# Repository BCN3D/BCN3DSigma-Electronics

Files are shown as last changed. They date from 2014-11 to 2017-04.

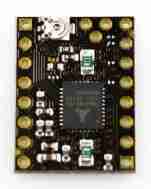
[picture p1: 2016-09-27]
Silent Stepper Driver 4L/Documentation/SilentStepStick-master/hardware/SilentStepStick_v11.jpg

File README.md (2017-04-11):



# BCN3D Electronics

This repository will hold all the information about the Electronics of the BCN3D Sigma.

As a declared Open Source organization, it's in our mission to release all the original design files to you to be able to learn, reuse and improve. Open Source not only means code, it also concerns hardware.

We've managed to design and manufacture our custom Electronics for the BCN3D Sigma in many ways thanks to the community and other Open Source Hardware projects.
BCN3D Electronics is a mashup between the [Ultimaker 2 Board](https://github.com/Ultimaker/Ultimaker2) , the [Megatronics v3.0](http://reprap.org/wiki/Megatronics_3.0) and some others...

## Design concept

The BCN3D Electronics is intended to be modular and custom fitted in our BCN3D Sigma 3D printer and that's why we made some design decisions.

1. Stepper drivers out of the Mainboard. As the drivers generate quite a lot of heat, we've moved them nearest as possible to the corresponding stepper motor. If one fails, you just have to replace a cheap stepper driver board. This way, we've managed to fit an entire electronics system without a fan.
2. FFC's everywhere. The BCN3D Sigma is an Independent Dual Extruder Printer so the Electronics supports 6  Axis of movement. Thats a lot of wires and wires takes some precious space. We decided to go with a Flat Flexible Cable solution that keeps things organized and it's faster to assemble.
3. 24VDC Power Supply. The performance improves as the whole Electronics run cooler while maintaining a very low voltage system.  
4. Full Color Resistive Touch Screen. The electronics is compatible with 4D Systems Displays out of the box. We think the user should interact with an intuitive interface to be able to use the printer easily even without previous experience in 3D printing.

## Boards

+ **Mainboard:** This board holds the microcontroller, the 5V switching power supply, the power outputs and the thermistor inputs. It has a USB interface for upgrading the firmware and communicating with the printer via serial port.
+ **Stepper Driver:** We carry the well-known DRV8825 stepper driver from Texas Instruments. It's able to supply plenty of power for all the types of stepper motors in the BCN3D Sigma.
+ **Extruder Board:** It's a simple interconnection board between the Mainboard and the components of the hotend assembly. With just one Flat Flexible Cable you the microcontroller has control over the hotend, the thermistor and endstop readings and the layer fan.
+ **Heated Bed:** As the platform size of the BCN3D Sigma is quite big, we've made a custom A4 size heated bed to achieve the performance required. It can heat up to 100ºC in about 6-8 minutes and keep that temperature for long period of times.
+ **SD Reader:** We've design our own SD Reader module with better signal integrity and better power supply requirements. This board has been designed entirely in [KiCAD Open Source software](http://kicad-pcb.org/). 

## Production

We strongly believe that using high quality components has an effect on the electronics performance as well as in the printer performance.

This is why we ensure components quality and control of the production process by designing and manufacturing in Barcelona. In this manner we iterate faster, reducing time to market.

Being in control of all the supply chain allows us to optimize designs and reduce costs.

## Contributing

If you own a BCN3D Sigma and electronics is your thing, feel free to post an [issue](https://github.com/BCN3D/BCN3D-Electronics/issues). We know this is still an 8-bit platform but we're working on optimizing it to the max and thinking in the next generation of 3D Printing Electronics. Always Open Source.

### License

Under the **LICENSE** folder you'll find all the information about the license. We've chosen CERN Open Hardware License and you must follow the guidelines as we had. All the documentation is available to you to study it, modify it and share it.
In addition, if modifications are made and distributed, it must be under the same licence conditions – this is the ‘persistent’ nature of the licence, which ensures that the whole community will continue benefiting from improvements, in the sense that everyone will in turn be able to make modifications to these improvements.

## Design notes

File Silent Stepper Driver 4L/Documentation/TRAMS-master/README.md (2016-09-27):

# TRAMS
TRINAMIC ReRrap Arduino Mega Shield, Reference Design for 3D Printing with 4x TMC5130

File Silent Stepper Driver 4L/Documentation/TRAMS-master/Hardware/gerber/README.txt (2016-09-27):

TRAMS v0.91

4 Layer PCB
35 um Copper
1.6mm thickness

Do not buy and assemble D2, D4, D6. 
Only D5 is needed.

Do not assemble all THT parts but ship them with the PCBs.

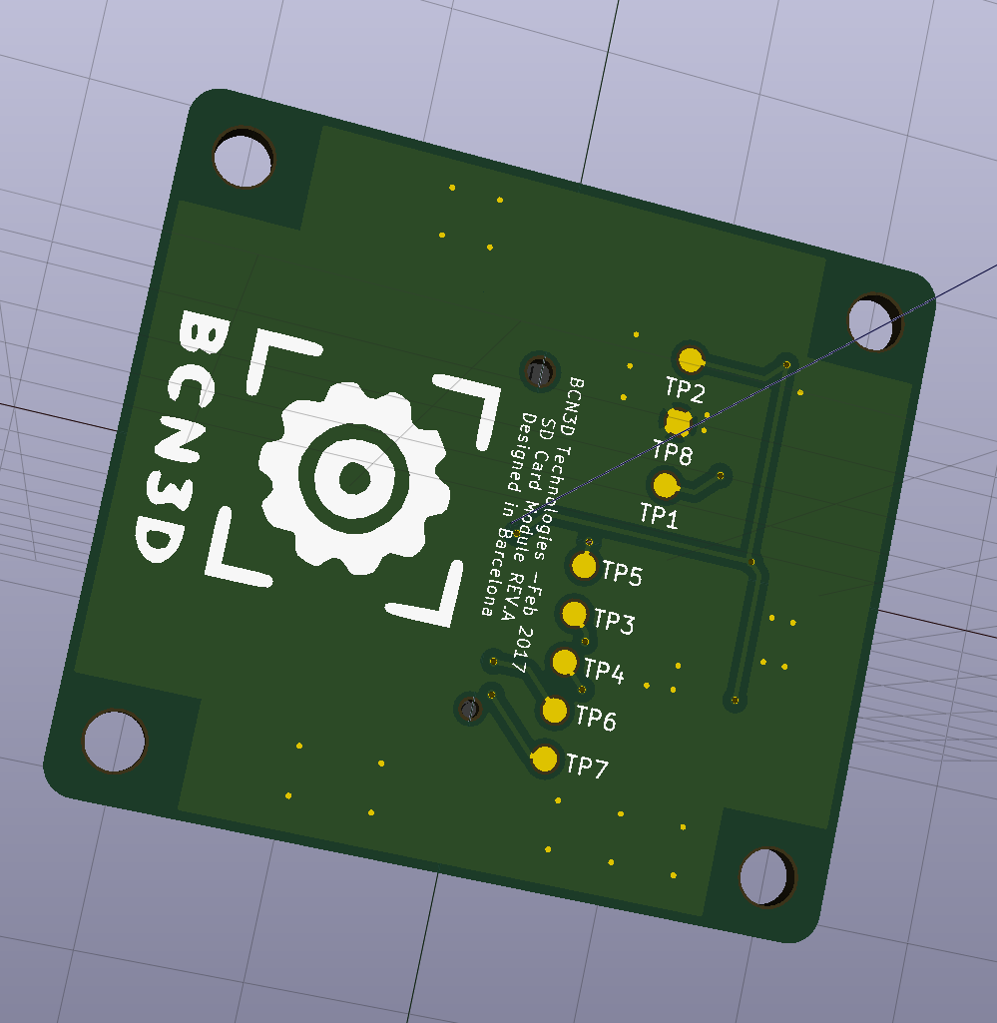
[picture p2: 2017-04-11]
SD Reader/IMG/3D_Back.PNG

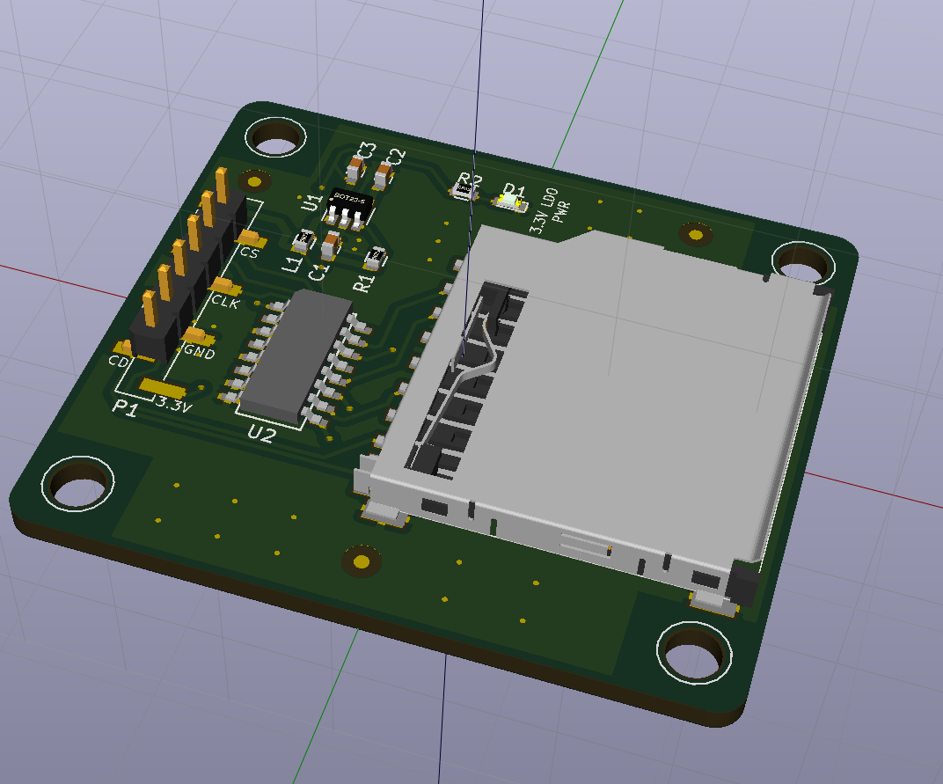
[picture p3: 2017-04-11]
SD Reader/IMG/3D_Front.PNG

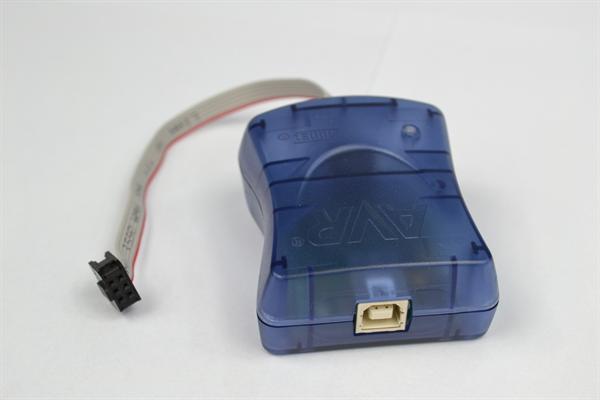
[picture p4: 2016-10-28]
img/avrispmkii.jpg

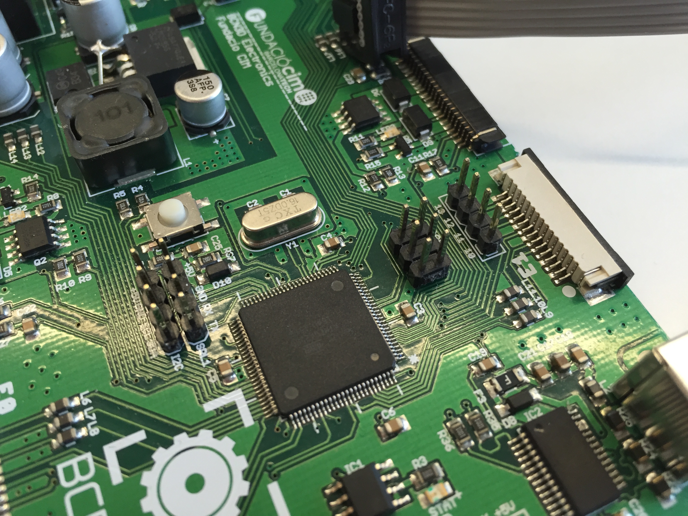
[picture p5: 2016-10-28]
img/mainboard.JPG

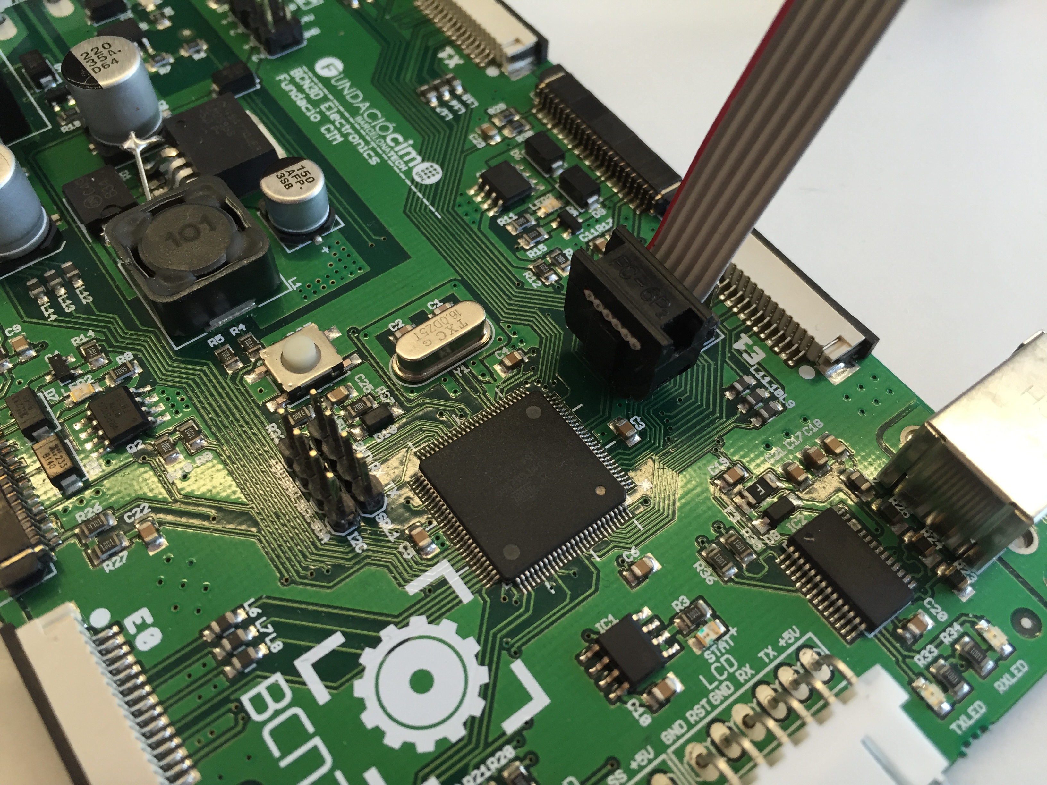
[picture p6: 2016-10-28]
img/mainboardwithcable.JPG

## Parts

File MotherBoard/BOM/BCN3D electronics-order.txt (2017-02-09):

Order list for C:/Users/mcobler/Documents/eagle/BCN3D Electronics/MotherBoard/BCN3D electronics.sch
Exported from EAGLE with DesignLink

Quantity	Value	Package	Order code	Manufacturer	Manuf. Code	Availability	Price (from)	Description
2		JP2Q	unknown					
5		1X04	unknown					
1	ATMEGA2560-16AU	QFP50P1600X1600X120-100N	1288330	ATMEL	ATMEGA2560-16AU	640	8.67	ATMEL - ATMEGA2560-16AU - MCU, 8BIT, ATMEGA, 16MHZ, TQFP-100
2	22p	C0805	2332763	AVX	08055A220KAT2A	38475	0.02	AVX - 08055A220KAT2A - COND, CERÁ MULT, C0G/NP0, 22PF, 50V 0805
8	100n	C0805	499687	AVX	08055C104KAT2A	231426	0.0113	AVX - 08055C104KAT2A - COND, CERÁ MULT, X7R, 100NF, 50V, 0805
1	150UF	CAPAE660X610N	1539463	PANASONIC ELECTRONIC COMPONENTS	EEEFP1A151AP	1011	0.158	PANASONIC ELECTRONIC COMPONENTS - EEEFP1A151AP - COND, ELEC ALUM, 150UF, 10V, SMD
1	220u	UD-8X10_NICHICON	2326175	PANASONIC ELECTRONIC COMPONENTS	EEE1VA221UAP	2654	0.176	PANASONIC ELECTRONIC COMPONENTS - EEE1VA221UAP - COND, ELEC ALUM, 220UF, 35V, SMD
5	0.1u	C0805	499687	AVX	08055C104KAT2A	231426	0.0113	AVX - 08055C104KAT2A - COND, CERÁ MULT, X7R, 100NF, 50V, 0805
2	100u	UD-8X10_NICHICON	1244377	PANASONIC ELECTRONIC COMPONENTS	EEEFC1V101AP	2580	0.292	PANASONIC ELECTRONIC COMPONENTS - EEEFC1V101AP - COND, ELEC ALUM, 100UF, 35V, SMD
2	10u	C1210K	1735537	MURATA	GRM32ER7YA106KA12L	7393	0.556	MURATA - GRM32ER7YA106KA12L - COND, CERÁ MULT, X7R, 10UF, 35V, 1210
1	4.7u	C0805	1833871	AVX	06035C103JAT2A	39173	0.0216	AVX - 06035C103JAT2A - COND, CERÁ MULT, X7R, 10NF, 50V, 0603
2	10n	C0805	499225	AVX	08055C103KAT2A	135923	0.0113	AVX - 08055C103KAT2A - COND, CERÁ MULT, X7R, 10NF, 50V, 0805
1		SMC	9557377	ON SEMICONDUCTOR	MBRS340T3G	44451	0.135	ON SEMICONDUCTOR - MBRS340T3G - DIODE, SCHOTTKY, 3A, 40V, SMC
7	MBRA140	SMA-DIODE	1843670	DIODES INC.	B140-13-F	52776	0.0309	DIODES INC. - B140-13-F - DIODO, SCHOTTKY, 40V, 1A, DO-214AC
2	MBR0520LT	SOD123	2284096	PANASONIC ELECTRONIC COMPONENTS	DA22F2100L	3048	0.0921	PANASONIC ELECTRONIC COMPONENTS - DA22F2100L - DIODO, 200V, 1A, MINI2-F4-B
6	FFC_15V_90G_1MM	TE_FFC_CON1MM	unknown					
1	IN_PTC	PTC-1206	1829472	SCHURTER	3413.0329.22	-2	0.437	SCHURTER - 3413.0329.22 - FUSIBLE, SMD, UST 1206, 12A
1		MICROBUILDER_1206_PTC	1596993	LITTELFUSE	1206L050YR	16086	0.164	LITTELFUSE - 1206L050YR - FUSE, RESETTABLE, 1206, 6V, 500MA
3	FIDUCIAL	FIDUCIAL_1MM	unknown					
2	PC4WAY	MOLEX_MINIFIT-JR	9963553	MOLEX	39303045	843	0.527	MOLEX - 39303045 - MACHO, MINI-FIT, R/A, SIL, 4 VÍAS
2	FFC_20V_90G_1MM3	FCI_20WAY_1MM_3ST	unknown					
1	LM358D	SO08	1564327	STMICROELECTRONICS	LM2904DT	140967	0.122	STMICROELECTRONICS - LM2904DT - AMP OP, DUAL, 1,1MHZ, 0,6V/µS, 8SOIC
1	FT232RL	SSOP28	1146032	FTDI	FT232RL	8169	2.52	FTDI - FT232RL - IC, USB A UART, SMD, 28SSOP
1	AVR_SPI_PRG_6NS	2X3-NS	unknown					
1	G5L	G5LE	1455502	OMRON ELECTRONIC COMPONENTS	G5LA-1 5DC	64238	0.421	OMRON ELECTRONIC COMPONENTS - G5LA-1 5DC - RELAY, PCB, SPDT, 5VDC, 10A
1	100u	SSR1260	2396102	BOURNS	SRR1260-101M	267	0.746	BOURNS - SRR1260-101M - INDUCTOR, POWER, SHLD, 100UH, 20%, 1.7A
1	1800367 Ferrite Bead	M0805	1800367	WURTH ELEKTRONIK	742792012	2729	0.132	WURTH ELEKTRONIK - 742792012 - INDUCTOR, 8000UOHM, 4A, 0805
18		0805	unknown					
2		1X06	unknown					
5	Blue	CHIPLED_0805	1716765	MULTICOMP	OVS-0803	53667	0.142	MULTICOMP - OVS-0803 - LED, 0805, AZUL, 100MCD, 465NM
1		TO263-5	1469193	TEXAS INSTRUMENTS	LM2595S-5.0/NOPB	504	2.14	TEXAS INSTRUMENTS - LM2595S-5.0/NOPB - IC, DC/DC CONVERTER, 1A, SMD
1	OSHW-LOGOM	OSHW-LOGO-M	unknown					
3	MOSFET-N	SOIC8	1551903	INTERNATIONAL RECTIFIER	IRF8736PBF	2194	0.311	INTERNATIONAL RECTIFIER - IRF8736PBF - MOSFET, N SO-8
3	BC817	SOT23-3	1081225	NXP	BC817-40	166946	0.0144	NXP - BC817-40 - TRANSISTOR, NPN, 45 V, 0,5A, SOT23
3		SOT23	1081307	NXP	BSH103,215	12726	0.117	NXP - BSH103,215 - MOSFET, N, 30V, 0.85A, SOT-23
3	5.6k	M0805	2008389	BOURNS	CR0805-JW-102ELF	25857	0.0114	BOURNS - CR0805-JW-102ELF - RESISTENCIA, 0805, 1K, 5%, 1/8W
2	1K	R0805	2008389	BOURNS	CR0805-JW-102ELF	25857	0.0114	BOURNS - CR0805-JW-102ELF - RESISTENCIA, 0805, 1K, 5%, 1/8W
2	4.7k	M0805	2008390	BOURNS	CR0805-JW-103ELF	16397	0.0104	BOURNS - CR0805-JW-103ELF - RESISTENCIA, 0805, 10K, 5%, 1/8W
15	1K	M0805	2008389	BOURNS	CR0805-JW-102ELF	25857	0.0114	BOURNS - CR0805-JW-102ELF - RESISTENCIA, 0805, 1K, 5%, 1/8W
3	10K	M0805	2008390	BOURNS	CR0805-JW-103ELF	16397	0.0104	BOURNS - CR0805-JW-103ELF - RESISTENCIA, 0805, 10K, 5%, 1/8W
5	4.7K	M0805	2008383	BOURNS	CR0805-FX-4701GLF	39067	0.0156	BOURNS - CR0805-FX-4701GLF - RESISTENCIA, 4K7, 0.125W, 1%
3	VARISTORCN0805	CT/CN0805	1057218	LITTELFUSE	V5.5MLA0805LH	3610	0.178	LITTELFUSE - V5.5MLA0805LH - VARISTOR, 0805, 5.5VAC
1	330	M0805	2008390	BOURNS	CR0805-JW-103ELF	16397	0.0104	BOURNS - CR0805-JW-103ELF - RESISTENCIA, 0805, 10K, 5%, 1/8W
1	10k	M0805	2008390	BOURNS	CR0805-JW-103ELF	16397	0.0104	BOURNS - CR0805-JW-103ELF - RESISTENCIA, 0805, 10K, 5%, 1/8W
1	5.6K	R0805	2008383	BOURNS	CR0805-FX-4701GLF	39067	0.0156	BOURNS - CR0805-FX-4701GLF - RESISTENCIA, 4K7, 0.125W, 1%
1	SPST	EVQ-Q2	9962913	PANASONIC ELECTRONIC COMPONENTS	EVQQ2503W	6869	0.133	PANASONIC ELECTRONIC COMPONENTS - EVQQ2503W - SWITCH, SPNO, SMD
2	green	CHIPLED_0805	2322081	WURTH ELEKTRONIK	150080VS75000	5253	0.116	WURTH ELEKTRONIK - 150080VS75000 - LED, 0805, B GREEN, 40MCD, 570NM
1	SHORTT5	SHORT_TOP-50	unknown					
1	Orange	CHIP-LED0805	2290332	KINGBRIGHT	KP-2012SECK	2121	0.0662	KINGBRIGHT - KP-2012SECK - LED, 0805, 250MCD, ORANGE
20	TPB2,54	B2,54	unknown					
1	USB+SHIELD	USB-B-PTH	1463095	MOLEX	67068-8000	2831	0.556	MOLEX - 67068-8000 - USB, 2.0 TIPO B, HEMBRA, SMT
1		JP1	unknown					
1		HC49US	1842216	TXC	9B-16.000MAAJ-B	8167	0.172	TXC - 9B-16.000MAAJ-B - XTAL, 16.000MHZ, 18PF, HC-49S

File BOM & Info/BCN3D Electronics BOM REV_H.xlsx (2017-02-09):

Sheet: MotherBoard
Quantity | Value | Designador | Package | Order code | Manufacturer | Manuf. Code | Availability | Price (from) | Description
2 | 10n | C18, C25 | C0805 | 499225 | AVX | 08055C103KAT2A | 135923 | 0.0113 | AVX - 08055C103KAT2A - COND, CERÁ MULT, X7R, 10NF, 50V, 0805
11 | 100n | C3, C4, C5, C6, C10, C19, C20, C21, C22, C23, C24 | C0805 | 499687 | AVX | 08055C104KAT2A | 231426 | 0.0113 | AVX - 08055C104KAT2A - COND, CERÁ MULT, X7R, 100NF, 50V, 0805
3 | VARISTORCN0805 | R23, R24, R25 | CT/CN0805 | 1057218 | LITTELFUSE | V5.5MLA0805LH | 3610 | 0.178 | LITTELFUSE - V5.5MLA0805LH - VARISTOR, 0805, 5.5VAC
3 | BC817 | Q4, Q5, Q9 | SOT23-3 | 1081225 | NXP | BC817-40 | 166946 | 0.0144 | NXP - BC817-40 - TRANSISTOR, NPN, 45 V, 0,5A, SOT23
3 | BSH103 | Q6, Q7, Q8 | SOT23 | 1081307 | NXP | BSH103,215 | 12726 | 0.117 | NXP - BSH103,215 - MOSFET, N, 30V, 0.85A, SOT-23
1 | FT232RL | IC2 | SSOP28 | 1146032 | FTDI | FT232RL | 8169 | 2.52 | FTDI - FT232RL - IC, USB A UART, SMD, 28SSOP
2 | 100u | C12, C13 | UD-8X10_NICHICON | 2326148 | PANASONIC ELECTRONIC COMPONENTS | EEE1HA101UAP | 2580 | 0.292 | PANASONIC ELECTRONIC COMPONENTS - EEE1HA101UAP - COND, ELEC ALUM, 100UF, 50V, SMD
1 | ATMEGA2560-16AU | IC5 | QFP50P1600X1600X120-100N | 1288330 | ATMEL | ATMEGA2560-16AU | 640 | 8.67 | ATMEL - ATMEGA2560-16AU - MCU, 8BIT, ATMEGA, 16MHZ, TQFP-100
1 | G5L | K1 | G5LE | 1455502 | OMRON ELECTRONIC COMPONENTS | G5LA-1 5DC | 64238 | 0.421 | OMRON ELECTRONIC COMPONENTS - G5LA-1 5DC - RELAY, PCB, SPDT, 5VDC, 10A
1 | USB+SHIELD | USB+SHIELD | USB-B-PTH | 1463095 | MOLEX | 67068-8000 | 2831 | 0.556 | MOLEX - 67068-8000 - USB, 2.0 TIPO B, HEMBRA, SMT
1 | LM2595S | IC4 | TO263-5 | 1469193 | TEXAS INSTRUMENTS | LM2595S-5.0/NOPB | 504 | 2.14 | TEXAS INSTRUMENTS - LM2595S-5.0/NOPB - IC, DC/DC CONVERTER, 1A, SMD
1 | 150UF | C7 | CAPAE660X610N | 1539463 | PANASONIC ELECTRONIC COMPONENTS | EEEFP1A151AP | 1011 | 0.158 | PANASONIC ELECTRONIC COMPONENTS - EEEFP1A151AP - COND, ELEC ALUM, 150UF, 10V, SMD
3 | MOSFET-N | Q1, Q2, Q3 | SOIC8 | 1551903 | INTERNATIONAL RECTIFIER | IRF8736PBF | 2194 | 0.311 | INTERNATIONAL RECTIFIER - IRF8736PBF - MOSFET, N SO-8
1 | LM358DRG3 | IC1 | SO08 | 2342290 | TEXAS INSTRUMENTS | LM358DRG3 | 140967 | 0.122 | TEXAS INSTRUMENTS LM358DRG3 OP-AMP, GENERAL PURPOSE, 700KHZ, SOIC-8
1 | INA139 | U1 | SOT23-5 | 2435757 | TEXAS INSTRUMENTS | INA139NA/250 |  |  | Amplificador de Detección de Corriente, Common-Mode Voltage, 1, 10 µA, SOT-23, 5, -55 °C, 125 °C
1 | LM311D | IC3 | SO08 | 2293183 | TEXAS INSTRUMENTS | LM311DR |  |  | Comparador Analógico, Rail to Rail, Alta Velocidad, 1, 115 ns, 3.5V a 30V, SOIC, 8
1 | 5V FUSE | F3 | MICROBUILDER_1206_PTC | 1596993 | LITTELFUSE | 1206L050YR | 16086 | 0.164 | LITTELFUSE - 1206L050YR - FUSE, RESETTABLE, 1206, 6V, 500MA
5 | Blue | PWR24, PWR5, LED1, LED2, LED3 | CHIPLED_0805 | 1716765 | MULTICOMP | OVS-0803 | 53667 | 0.142 | MULTICOMP - OVS-0803 - LED, 0805, AZUL, 100MCD, 465NM
3 | 10u | C9, C11, C15 | M0805 | 2320856 | MULTICOMP | MC0805X106K160CT |  |  | Condensador de Cerámica Multicapa, Serie MC, 10 µF, ± 10%, X5R, 16 V, 0805 [Métrica 2012]
2 | 10u | C14,C16 | C1210K | 1735537 | MURATA | GRM32ER7YA106KA12L | 7393 | 0.556 | MURATA - GRM32ER7YA106KA12L - COND, CERÁ MULT, X7R, 10UF, 35V, 1210
1 | 1800367 Ferrite Bead | L2 | M0805 | 1800367 | WURTH ELEKTRONIK | 742792012 | 2729 | 0.132 | WURTH ELEKTRONIK - 742792012 - INDUCTOR, 8000UOHM, 4A, 0805
1 | IN_PTC | F1 | PTC-1206 | 1829472 | SCHURTER | 3413.0329.22 | -2 | 0.437 | SCHURTER - 3413.0329.22 - FUSIBLE, SMD, UST 1206, 12A
1 | 4.7u | C17 | C0805 | 2281018 | AVX | 0805YC475KAT2A | 39173 | 0.0216 | AVX - 0805YC475KAT2A - COND, CERÁ MULT, X7R, 4,7UF, 16V, 0805
1 | 16MHZ CRYSTAL | Y1 | HC49US | 1842216 | TXC | 9B-16.000MAAJ-B | 8167 | 0.172 | TXC - 9B-16.000MAAJ-B - XTAL, 16.000MHZ, 18PF, HC-49S
7 | B140 | D2, D3, D4, D5, D6, D7, D9 | SMA-DIODE | 1843670 | DIODES INC. | B140-13-F | 52776 | 0.0309 | DIODES INC. - B140-13-F - DIODO, SCHOTTKY, 40V, 1A, DO-214AC
1 | 0.01 | RSHUNT | 2512 | 1435947 | BOURNS | CRA2512-FZ-R010ELF |  |  | Resistencia Detección de Corriente SMD, Serie CR, 0.01 ohm, 3 W, ± 1%, 2512 [Métrica 6432]
7 | 4.7K | R4, R5, R16, R17, R26, R28, R29 | M0805 | 2008383 | BOURNS | CR0805-FX-4701GLF | 39067 | 0.0156 | BOURNS - CR0805-FX-4701GLF - RESISTENCIA, 4K7, 0.125W, 1%
4 | 5.6K | R2, R8, R11, R38 | R0805 | 2447693 (http://es.farnell.com/multicomp/mcwr08x5601ftl/resist-pel-gru-5-6kohm-1-0-125w/dp/2447693) | MULTICOMP | MCWR08X5601FTL | 39067 | 0.0156 | MULTICOMP MCWR08X5601FTL RESIST, PELÍ GRU, 5.6KOHM, 1%, 0.125W
18 | 1K | R3, R6, R9, R12, R14, R15, R19, R20, R21, R22, R27, R30, R33, R34, R35, R36, R39, R43, R45, R46, R47 | M0805 | 2008389 | BOURNS | CR0805-JW-102ELF | 25857 | 0.0114 | BOURNS - CR0805-JW-102ELF - RESISTENCIA, 0805, 1K, 5%, 1/8W
9 | 10K | R1, R7, R10, R13, R18, R31, R37, R40, R42 | M0805 | 2008390 | BOURNS | CR0805-JW-103ELF | 16397 | 0.0104 | BOURNS - CR0805-JW-103ELF - RESISTENCIA, 0805, 10K, 5%, 1/8W
1 | 20K | R41 | M0805 | 2447603 | MULTICOMP | MCWR08X2002FTL |  |  | Resistencia tipo Chip SMD, Película Gruesa, Serie MCWR, 20 kohm, 125 mW, ± 1%, 150 V
1 | 100K | R44 | M0805 | 2447551 | MULTICOMP | MCWR08X1003FTL |  |  | Resistencia tipo Chip SMD, Película Gruesa, Serie MCWR, 100 kohm, 125 mW, ± 1%, 150 V
1 | 330 | R32 | M0805 | 2447638 | MULTICOMP | MCWR08X3300FTL | 16397 | 0.0104 | MULTICOMP MCWR08X3300FTL Resistencia de Película Gruesa SMD, Serie MCWR, 330 ohm, 125 mW, ± 1%, 150 V
2 | MBR0520LT | D8, D10 | SOD123 | 9556915 | ON SEMICONDUCTOR | MBR0520LT1G | 3048 | 0.0921 | ON SEMICONDUCTOR MBR0520LT1G DIODE, SCHOTTKY, 0.5A, 20V, SMC
1 | Orange | STAT | CHIP-LED0805 | 2290332 | KINGBRIGHT | KP-2012SECK | 2121 | 0.0662 | KINGBRIGHT - KP-2012SECK - LED, 0805, 250MCD, ORANGE
2 | green | TXLED, RXLED | CHIPLED_0805 | 2322081 | WURTH ELEKTRONIK | 150080VS75000 | 5253 | 0.116 | WURTH ELEKTRONIK - 150080VS75000 - LED, 0805, B GREEN, 40MCD, 570NM
1 | 220u | C8 | UD-8X10_NICHICON | 2326175 | PANASONIC ELECTRONIC COMPONENTS | EEE1VA221UAP | 2654 | 0.176 | PANASONIC ELECTRONIC COMPONENTS - EEE1VA221UAP - COND, ELEC ALUM, 220UF, 35V, SMD
2 | 22p | C1, C2 | C0805 | 2332763 | AVX | 08055A220KAT2A | 38475 | 0.02 | AVX - 08055A220KAT2A - COND, CERÁ MULT, C0G/NP0, 22PF, 50V 0805
1 | 100u | L1 | SSR1260 | 2396102 | BOURNS | SRR1260-101M | 267 | 0.746 | BOURNS - SRR1260-101M - INDUCTOR, POWER, SHLD, 100UH, 20%, 1.7A
1 | Diode | D1 | SMC | 9557377 | ON SEMICONDUCTOR | MBRS340T3G | 44451 | 0.135 | ON SEMICONDUCTOR - MBRS340T3G - DIODE, SCHOTTKY, 3A, 40V, SMC
1 | SPST | RST | EVQ-Q2 | 9962913 | PANASONIC ELECTRONIC COMPONENTS | EVQQ2503W | 6869 | 0.133 | PANASONIC ELECTRONIC COMPONENTS - EVQQ2503W - SWITCH, SPNO, SMD
2 | PC4WAY | SUPPLY, HEATEDBED | MOLEX_MINIFIT-JR | 9963553 | MOLEX | 39303045 | 843 | 0.527 | MOLEX - 39303045 - MACHO, MINI-FIT, R/A, SIL, 4 VÍAS
2 | 2X4 PINHEADERS | 5V, 24V | JP2Q | - |  |  |  |  | 2X4 PINHEADERS
1 | 1X2 PINHEADER | VCC2 | 1X02 | 9729038 | FISCHER ELEKTRONIK | SL1.025.36Z |  |  | FISCHER ELEKTRONIK SL1.025.36Z MACHO, PIN, 2,54 MM,
1 | JUMPER | VCC2 | JUMPER | 4218152 | TE CONNECTIVITY / AMP | 0-0142270-3 |  |  | TE CONNECTIVITY / AMP 0-0142270-3 PUENTE, MÓDULO AMP, NGR, ESTAÑADO
4 | 1X4 PINHEADERS | SRL1, I2C, ADC | 1X04 | 9729038 | FISCHER ELEKTRONIK | SL1.025.36Z |  |  | FISCHER ELEKTRONIK SL1.025.36Z MACHO, PIN, 2,54 MM,
1 | 2X4 PINHEADERS RIGHT ANGLE | RGBLEDS | 2X04 | 0010883081 | MOLEX | A70216-0081 |  |  | 2.54mm Pitch C-Grid® Breakaway Header, High Profile, Dual Row, Right Angle, 8 Circuits, 6.10mm Mating Pin Length, Tin (Sn) Plating
6 | FFC_15V_90G_1MM | X0, E0, Z, E1, X1, Y0 | FFC CONNECTOR | ZF1-15-01-T-WT | SAMTEC | ZF1-15-01-T-WT
2 | FFC_20V_90G_1MM3 | HOTEND0, HOTEND1 | WURTH_20WAY_1MM_3ST | 1641903 | WURTH ELEKTRONIK | 68612014422 | 610 | 1.73 | Conector de Placa FFC / FPC, ZIF, 20 Contactos, Macho, 1 mm, Montaje Superficial, Planta
1 | AVR_SPI_PRG_6NS | ICSP | 2X3-NS | - |  |  |  |  | 2X3 PINHEADER
19 | Ferrite bead | L3, L4, L5, L6, L7, L8, L9, 10, L11, L12, L13, L14, L15, L16, L17, L18, L19, L20,L21 | 805 | 1800367 | WURTH ELEKTRONIK
2 | RIGHT ANGLE CONNECTOR | SD, LCD | 1X06 | 1756799 | MOLEX |  |  |  | 2.54MM, 6WAY

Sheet: Stepper Driver - 4L
Qty | Value | Device | Package | Parts | MF | MPN | OC_FARNELL | DIGIKEY | Description
1 | 20K | TRIM_US-3223G | 3223G | ADJUST | VISHAY | TS53YL203MR10 | 1141475 | - | POTENTIOMETER
1 | 22n | C-USC0603K | C0603K | C1 | MURATA | GCM188R72A223KA37D | 2494195 | - | CAPACITOR, American symbol
6 | 100n | C-USC0603K | C0603K | C2, C3, C4, C6, C7, C9 | AVX | 06035C104KAT2A | 1301804 | - | CAPACITOR, American symbol
1 | 100u | CPOL-USUD-6,3X7,7 | UD-6,3X7,7_NICHICON | C5 | PANASONIC ELECTRONIC COMPONENTS | EEEFT1V101AP | 1868417 | - | POLARIZED CAPACITOR, American symbol
1 | 4.7u | C-USC1210 | C1210 | C8 | KEMET | C1210X475K5RACTU | 1414067 | - | CAPACITOR, American symbol
1 | 470n | C-USC0603K | C0603K | C10 | MURATA | GRM188R71C474KA88D | 1828893 | - | CAPACITOR, American symbol
1 | 4.7u | C-USC0805 | C0805 | C11 | AVX | 0805YC475KAT2A | 1657937 | - | CAPACITOR, American symbol
1 | PD3S160 | PD3S160 | POWERDI323 | D1 | DIODES INC. | PD3S160-7 | 1843697 | - | 1.0A SURFACE MOUNT SCHOTTKY BARRIER RECTIFIER POWERDI ® 323
1 |  | DIODE-MINIMELF | MINIMELF | D2 | NXP | PMLL4448 | 1097279 | - | DIODE
1 | FFC_15V_90G_1MM | FFC_15V_90G_1MM | TE_FFC_CON1MM | FFC2 | SAMTEC | ZF1-15-01-T-WT | - | - | SAMTEC FFC CONNECTOR 15 WAY 1MM PITCH. HORIZONTAL
1 | TMC2130-LA | TMC2130-LA | TMC_QFN36_0.5_5.0X6.0 | IC1 | TRINAMIC | TMC2130-LA | - | 1460-1130-1-ND | Universal high voltage driver for two-phase bipolar stepper motor
1 |  | M06 | JST-6-PTH | MOTOR | JST (JAPAN SOLDERLESS TERMINALS) | S6B-PH-K-S (LF)(SN) | 9492500 | - | Header 6
2 | 0R11 | R-US_R0805 | R0805 | R1, R2 | SUSUMU | RL1220S-R11-F | - | RL12S.11FCT-ND | RESISTOR, American symbol
1 | 20K | R-US_R0603 | R0603 | R3 | MULTICOMP | MC0201L6F2002SE. | 1837767 | - | RESISTOR, American symbol
1 | 4.7K | R-US_R0603 | R0603 | R4 | PANASONIC ELECTRONIC COMPONENTS | ERJP06F4701V | 1750763 | - | RESISTOR, American symbol
1 | 1K | R-US_R0603 | R0603 | R6 | BOURNS | CR0805-JW-102ELF | 2008389 | - | RESISTOR, American symbol
3 |  | SJ | SJ | SJ1, SJ2, SJ3 |  |  | - | - | SMD solder JUMPER
1 |  | SJ2W | SJ_2 | SJ4 |  |  | - | - | SMD solder JUMPER
1 |  | M03PTH | 1X03 | SMAEX |  |  | - | - | Header 3. NON POPULATED
1 |  | JST_2PIN-THM-RA | JST-PH-2-THM-RA | STOP1 | JST (JAPAN SOLDERLESS TERMINALS) | S2B-PH-K-S (LF)(SN) | 9491902 | - | JST 2-Pin Connectors of various flavors
3 | PTR1TP12R | PTR1TP12R | TP12R | TP1, TP2, TP3 |  |  | - | - | TEST POINT
3 | FIDUCIAL | FIDUCIAL | FIDUCIAL_1MM | U$2, U$3, U$4 |  |  | - | - | For use by pick and place machines to calibrate the vision/machine, 1mm

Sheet: Extruder Board
Qty | Value | Device | Package | Parts | Description | MF | MPN | OC_FARNELL | MOUSER
2 | 100nF | C-EUC0603K | C0603K | C1, C2 | CAPACITOR, European symbol | AVX | 06035C104KAT2A | 1301804 | -
1 | 330nF | C-EUC0805 | C0805 | C3 | CAPACITOR, European symbol | MURATA | GRM219R71H334KA88D | 1828951 | -
1 | LM3480IM4 | LM3480IM4 | SOT23-3 | U2 | Small package linear regulator | TEXAS INSTRUMENTS | LM3480IM3-12/NOPB | 1469099 | -
1 | 1K | R-US_R0603 | R0603 | L1 | FERRITA, INDUCTOR, 0603, 0,6 OHM, 0,2A | WURTH ELEKTRONIK | 74279266 | 1635693 | -
1 | MOSFET-NSOT323 | MOSFET-NSOT323 | SOT323 | Q2 | CJ2302:SMD MOSFET N-CH 20V-2.1A | NXP | PMF370XN,115 | 1758096 | -
1 | PD3S160 | PD3S160 | POWERDI323 | D1 | 1.0A SURFACE MOUNT SCHOTTKY BARRIER RECTIFIER POWERDI ® 323 | DIODES INC. | PD3S160-7 | 1843697 | -
1 | 5k23 | R-US_R0603 | R0603 | R3 | RESISTOR, American symbol | PANASONIC ELECTRONIC COMPONENTS | ERJ3EKF5231V | 2059380 | -
1 | 22.6K | R-US_R0603 | R0603 | R7 | Resistencia SMD Película Gruesa, Serie AEC-Q200 ERJ, 22.6 kohm, | PANASONIC | ERJ3EKF2262V | 2059438
1 | 200k | R-US_R0603 | R0603 | R5 | RESISTOR, American symbol | PANASONIC ELECTRONIC COMPONENTS | ERJ3EKF2003V | 2059509 | -
2 | 1k | R-US_R0603 | R0603 | R4, R6 | RESISTOR, American symbol | MULTICOMP | MCMR06X1001FTL | 2073348 | -
2 | 10k | R-US_R0603 | R0603 | R2, R8 | RESISTOR, American symbol | MULTICOMP | MCMR06X1002FTL | 2073349 | -
1 |  | JST_4PINPA | JST_PA_04 | CN1 |  | JST (JAPAN SOLDERLESS TERMINALS) | SM04B-PASS-TBT(LF)(SN) | 2399347 | -
1 | BC807W | BC807W | SOT323-BEC | Q1 | PNP Transistror | NXP | BC807W,115 | 2439010 | -
1 | 100 | R-US_R1210 | R1210 | R1 | Resistencia SMD de Tipo Chip, WF10P Series, 100 ohm | WALSIN | WF10P1000FTL | 2502767 | -
3 |  | JST_2MM_MALE | JST-2-SMD | CFAN, ENDSTOP, LFAN | Mates to single-cell LiPo batteries. | JST (JAPAN SOLDERLESS TERMINALS) | S2B-PH-SM4-TB(LF)(SN) | 9492615 | -
3 | FIDUCIAL | FIDUCIAL | FIDUCIAL_1MM | U$1, U$2, U$3 | For use by pick and place machines to calibrate the vision/machine, 1mm |  |  | - | -
1 | LM392MVSSOP8 | LM392MVSSOP8 | VSSOP8 | U3 | Low Power Operational Amplifier | TEXAS INSTRUMENTS | LM392DGKR (http://www.mouser.es/ProductDetail/Texas-Instruments/LM392DGKR/) | - | 595-LM392DGKR
1 | FFC_20V_90G_1MM3 | WURTH_20WAY_1MM_3ST | WURTH_20WAY_1MM_3ST | VERT_FFC1 | Conector de Placa FFC / FPC, ZIF, 20 Contactos, Macho, 1 mm, Montaje Superficial, Planta | WURTH ELEKTRONIK | 68612014422 | 1641903 | -
3 | TPB1,27 | TPB1,27 | B1,27 | 24V, 5V, GND | Test pad |  |  | - | -

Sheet: Heated Bed
Quantity | Value | Designador | Package | Order code | Manufacturer | Manuf. Code | Description
1 | Blue | LED1 | CHIPLED_0805 | 1716765 | MULTICOMP | OVS-0803 | MULTICOMP - OVS-0803 - LED, 0805, AZUL, 100MCD, 465NM
1 | PC4WAY | CON | MOLEX_MINIFIT-JR | 9963553 | MOLEX | 39303045 | MOLEX - 39303045 - MACHO, MINI-FIT, R/A, SIL, 4 VÍAS
1 | 5.6K | R1K | R0805 | 2447693 | MULTICOMP | MCWR08X5601FTL | MULTICOMP MCWR08X5601FTL RESIST, PELÍ GRU, 5.6KOHM, 1%, 0.125W
1 | Thermistor | THERM | R0806 | 2473599 | VISHAY | NTCS0805E3104SMT | VISHAY NTCS0805E3104SMT TERMISTOR, NTC, 100K, 1%, 0805

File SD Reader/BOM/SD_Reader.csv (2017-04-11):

Id | Identificador | Empaquetado | Cantidad | Identificador | Fabricante | MPN | Farnell | Digikey
1 | C2 | C_0603 | 1 | 10n
2 | C3,C1 | C_0603 | 2 | 1u
3 | D1 | LED_0603 | 1 | LED_ALT
4 | L1 | R_0603 | 1 | Ferrite_Bead_Small | WURTH ELEKTRONIK | 74279266 | 1635693
5 | R1,R2 | R_0603 | 2 | 1k | MULTICOMP | MCMR06X1001FTL | 2073348
6 | U1 | SOT-23-5 | 1 | LD3985M33R | TEXAS INSTRUMENTS | LP3985IM5-3.2/NOPB | 2463935
7 | U2 | SO-16-N | 1 | 4050 | TEXAS INSTRUMENTS | CD4050BD | 1740857
8 | CON1 | WE_SD_Card_P&P | 1 | SD_Card | WURTH ELEKTRONIK | 693063010911 | 2081360
9 | P1 | Pin_Header_Straight_1x08_Pitch2.54mm_SMD_Pin1Left | 1 | CONN_01X08

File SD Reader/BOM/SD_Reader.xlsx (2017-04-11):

Id | Identificador | Empaquetado | Cantidad | Identificador | Fabricante | MPN | Farnell | Digikey
1 | C2 | C_0603 | 1 | 10n | TDK | CGA3E2X7R1H103K080AA | 2354176
2 | C3,C1 | C_0603 | 2 | 1u | KEMET | C0603C105M4RACTU | 2680067
3 | C4 | C_1210 | 1 | 47u | MURATA | GRM32ER61A476KE20L | 1828818
4 | C5 | C_0805 | 1 | 10u | KEMET | C0805C106K8PACTU | 1463362
5 | D1 | LED_0603 | 1 | LED_ALT | WURTH ELEKTRONIK | 150060VS75000 | 2322073
6 | L1 | R_0603 | 1 | Ferrite_Bead_Small | WURTH ELEKTRONIK | 74279266 | 1635693
7 | R1,R2 | R_0603 | 2 | 1k | MULTICOMP | MCMR06X1001FTL | 2073348
8 | U1 | SOT-23-5 | 1 | LD3985M33R | TEXAS INSTRUMENTS | LP3985IM5-3.2/NOPB | 2463935
9 | U2 | SO-16-N | 1 | 74HC4050D | NEXPERIA | 74HC4050D | 1085272
10 | CON1 | WE_SD_Card_P&P | 1 | SD_Card | WURTH ELEKTRONIK | 693061010911 | 2081359
11 | P1 | Pin_Header_Straight_1x08_Pitch2.54mm_SMD_Pin1Left | 1 | CONN_01X08 | HARWIN | M20-8770642 | 1517384
12 | P2 | Pin_Header_Straight_1x02_Pitch2.54mm | 1 | NON POPULATED | NON POPULATED | NON POPULATED | -

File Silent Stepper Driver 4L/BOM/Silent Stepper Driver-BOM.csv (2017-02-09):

Qty | Value | Device | Package | Parts | Description | DATASHEET | DESCRIPTION | DISTRIBUTOR1 | DISTRIBUTOR2 | GEOMETRY_HEIGHT | MANUFACTURER | MF | MPN | OC_FARNELL | ORDERCODE-DISTRI1 | ORDERCODE-DISTRI2 | ORDERCODE-MANU1 | TP_SIGNAL_NAME | VALUE
1 | 20K | TRIM_US-3223G | 3223G | ADJUST | POTENTIOMETER |  |  |  |  |  |  | BOURNS | 3314G-2-203E | 2328481
1 | 22n | C-USC0603K | C0603K | C1 | CAPACITOR, American symbol |  |  |  |  |  |  | MURATA | GCM188R72A223KA37D | 2494195
6 | 100n | C-USC0603K | C0603K | C2, C3, C4, C6, C7, C9 | CAPACITOR, American symbol |  |  |  |  |  |  | AVX | 06035C104KAT2A | 1301804
1 | 100u | CPOL-USUD-6,3X7,7 | UD-6,3X7,7_NICHICON | C5 | POLARIZED CAPACITOR, American symbol |  |  |  |  |  |  | PANASONIC ELECTRONIC COMPONENTS | EEE1HA101UAP | 2326148
1 | 4.7u | C-USC1210 | C1210 | C8 | CAPACITOR, American symbol |  |  |  |  |  |  | KEMET | C1210X475K5RACTU | 1414067
1 | 470n | C-USC0603K | C0603K | C10 | CAPACITOR, American symbol |  |  |  |  |  |  | MURATA | GRM188R71C474KA88D | 1828893
1 | 4.7u | C-USC0805 | C0805 | C11 | CAPACITOR, American symbol |  |  |  |  |  |  | AVX | 0805YC475KAT2A | 1657937
1 | PD3S160 | PD3S160 | POWERDI323 | D1 | 1.0A SURFACE MOUNT SCHOTTKY BARRIER RECTIFIER POWERDI ® 323 |  |  |  |  |  |  | DIODES INC. | PD3S160-7 | 1843697
1 |  | DIODE-MINIMELF | MINIMELF | D2 | DIODE |  |  |  |  |  |  | NXP | PMLL4448 | 1097279
1 | FFC_15V_90G_1MM | FFC_15V_90G_1MM | TE_FFC_CON1MM | FFC2 |  |  |  |  |  |  |  |  |  | unknown
1 | TMC2130-LA | TMC2130-LA | TMC_QFN36_0.5_5.0X6.0 | IC1 | Universal high voltage driver for two-phase bipolar stepper motor, SPI, Step/Dir, QFN36(5x6) | http://www_trinamic_com/_scripts/download_php | Universal high voltage driver for two-phase bipolar stepper motor, SPI, Step/Dir, QFN36(5x6) | Digikey |  | 0_8mm | TRINAMIC |  |  | unknown | 1460-1130-1-ND |  | TMC2130-LA |  | TMC2130-LA
1 |  | M06 | JST-6-PTH | MOTOR | Header 6 |  |  |  |  |  |  | JST (JAPAN SOLDERLESS TERMINALS) | S6B-PH-K-S (LF)(SN) | 9492500
2 | 0R11 | R-US_R0805 | R0805 | R1, R2 | RESISTOR, American symbol |  |  |  |  |  |  | PANASONIC ELECTRONIC COMPONENTS | ERJ6BSFR11V | 2493027
1 | 20K | R-US_R0603 | R0603 | R3 | RESISTOR, American symbol |  |  |  |  |  |  | MULTICOMP | MC0201L6F2002SE. | 1837767
1 | 4.7K | R-US_R0603 | R0603 | R4 | RESISTOR, American symbol |  |  |  |  |  |  | PANASONIC ELECTRONIC COMPONENTS | ERJP06F4701V | 1750763
1 | 1K | R-US_R0603 | R0603 | R6 | RESISTOR, American symbol |  |  |  |  |  |  | BOURNS | CR0805-JW-102ELF | 2008389
3 |  | SJ | SJ | SJ1, SJ2, SJ3 | SMD solder JUMPER |  |  |  |  |  |  |  |  | unknown
1 |  | SJ2W | SJ_2 | SJ4 | SMD solder JUMPER |  |  |  |  |  |  |  |  | unknown
1 |  | M03PTH | 1X03 | SMAEX | Header 3 |  |  |  |  |  |  |  |  | unknown
1 |  | JST_2PIN-THM-RA | JST-PH-2-THM-RA | STOP1 | JST 2-Pin Connectors of various flavors |  |  |  |  |  |  | JST (JAPAN SOLDERLESS TERMINALS) | S2B-PH-K-S (LF)(SN) | 9491902
3 | PTR1TP12R | PTR1TP12R | TP12R | TP1, TP2, TP3 | TEST PIN |  |  |  |  |  |  |  |  | unknown
3 | FIDUCIAL | FIDUCIAL | FIDUCIAL_1MM | U$2, U$3, U$4 | For use by pick and place machines to calibrate the vision/machine, 1mm |  |  |  |  |  |  |  |  | unknown

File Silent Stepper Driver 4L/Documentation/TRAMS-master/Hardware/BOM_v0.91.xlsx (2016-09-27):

 |  | TRAMS 0.91 BOM
Item No. | Quantity | Reference | Part Type | Value | Description | Manufacturer | Manufacturer No. | Supplier | Supplier Part No. | Option
1 | 23 | C2, C3, C5, C7, C10, C12, C13, C14, C15, C16, C18, C20, C22, C24, C26, C28, C30, C32, C34, C36, C38, C39, C41 | 100nF/0603/10%/50V | 100nF
2 | 15 | R1, R2, R3, R19, R20, R21, R24, R26, R27, R28, R29, R33, R34, RL2, RL3 | 4.7k/0603/1%/0.1W | 4k7
3 | 9 | R4, R8, R9, R22, R23, R25, R30, R31, R32 | 100/0603/1%/0.1W | 100R
4 | 8 | R_PD6, R_PD7, R_PD8, R_PD9, R_PD10, R_PD11, R_PD12, R_PD13 | 100k/0603/1%/0.1W | 100k
5 | 8 | C1, C40, C44, C45, C46, C47, C48, C49 | 1nF/0603/10%/50V | 1nF
6 | 8 | C4, C6, C11, C19, C23, C27, C31, C35 | 4.7µF/0603/10%/35V | 4.7µF | X5R | Murata Electronics North America | GRM188R6YA475KE15D | Digikey | 490-7205-1-ND
7 | 8 | R5, R7, R10, R11, R13, R14, R16, R17 | 0R15/1206/1%/0.5W | 0R15 | ±100ppm/°C
8 | 5 | THERM0, THERM1, THERM2, VM0, VM1 | CONN HEADER EH TOP 2POS 2.5MM |  |  | JST | B2B-EH-A | Digikey | 455-1611-ND | Do not assemble
9 | 5 | E0_MOTOR, X_MOTOR, Y_MOTOR, Z_MOTOR_1, Z_MOTOR_2 | CONN HEADER EH TOP 4POS 2.5MM |  |  | JST | B4B-EH-A | Digikey | 455-1613-ND | Do not assemble
10 | 4 | TMC1, TMC2, TMC3, TMC5130 | TMC5130A-TA |  |  | TRINAMIC | TMC5130A-TA
11 | 4 | R6, R12, R15, R18 | 2.2/0603/1%/0.1W | 2R2
12 | 4 | C8, C17, C25, C33 | 22nF/0603/10%/50V | 22nF
13 | 4 | E0_ENDSTOP, X_ENDSTOP, Y_ENDSTOP, Z_ENDSTOP | CONN HEADER EH TOP 5POS 2.5MM |  |  | JST | B5B-EH-A | Digikey | 455-1614-ND | Do not assemble
14 | 1 | D5 | SMBJ24A |  | TVS DIODE 24VWM 38.9VC SMB |  |  | Digikey | SMBJ24AFSCT-ND
15 | 4 | C9, C21,C29, C37 | 470nF/0603/10%/50V | 470nF
16 | 3 | T1, T2, T3 | AON7508 |  | MOSFET N-CH 30V 26A 8DFN | Alpha & Omega Semiconductor Inc | AON7508 | Digikey | 785-1504-1-ND
17 | 3 | D_HB, D_HB1, D_HB2 | MSS1P6 |  | DIODE SCHOTTKY 60V 1A MICROSMP | Vishay Semiconductor Diodes Division | MSS1P6-M3/89A | Digikey | MSS1P6-M3/89AGICT-ND
18 | 3 | LED1, LED4, LED6 | LED/0603/RED | RED | 2mA/1.8V | OSRAM Opto Semiconductors Inc | LS L29K-G1J2-1-Z | Digikey | 475-2506-1-ND
19 | 2 | LED2, LED3 | LED/0603/GREEN | GREEN | 2mA/1.7V | OSRAM Opto Semiconductors Inc | LG L29K-G2J1-24-Z | Digikey | 475-2709-1-ND
20 | 3 | IC1, IC2, IC6 | SN74LVC3G17DCUR |  | Schmitt-Trigger | Texas Instruments | SN74LVC3G17DCUR | Digikey | 296-18818-1-ND
21 | 2 | C42, C43 | 1000µF/20%/35V | 1000µF | Radial Cap AL | United Chemi-Con | EKYB350ELL102MJ30S | Digikey | 565-3918-ND | Do not assemble
22 | 2 | F1, F2 | FUSE HOLDER RADIAL 250V 6.3A PCB |  |  | Littelfuse Inc | 56000001009 | Digikey | WK6235-ND | Do not assemble
23 | 3 | EX_0, FAN, HEATBED | RIA_AKL_220_2_PINS |  |  | METZ Connect | 31220102 |  |  | Do not assemble
24 | 1 | MAIN_IN | RIA_AKL_220_4_PINS |  |  | METZ Connect | 31220104 |  |  | Do not assemble
25 | 1 | S1 | SWITCH TACTILE SPST-NO 0.05A 24V |  | 6mm x 6mm | Omron Electronics Inc-EMC Div | B3F-1000 | Digikey | SW400-ND | Do not assemble
26 | 1 | XTAL | SM77H 16MHz | 16MHz | Oscillator | CTS-Frequency Controls | CB3-3I-16M0000 | Digikey | CTX304CT-ND
27 | 1 | - | FUSE BOARD MNT 10A 250VAC RADIAL | 10A | Fuse | Littelfuse Inc | 37421000000 | Digikey | WK4071CT-ND | Do not assemble
28 | 1 | - | FUSE BOARD MOUNT 5A 250VAC RAD | 5A | Fuse | Littelfuse Inc | 37315000000 | Digikey | WK3063CT-ND | Do not assemble
29 | 8 | I2C, SERVO, +5V, GND, AUX-1, AUX-3 | Header 4 Positions | 4 POS | Pitch 0.1"/Contact length 5.8mm/4 Pos/1 Row | MPE Connector | 087-1-004-0-F-XS0-1080 |  |  | Do not assemble
30 | 2 | AUX-2 | Header 5 Positions | 5 POS | Pitch 0.1"/Contact length 5.8mm/5 Pos/1 Row | MPE Connector | 087-1-005-0-F-XS0-1080 |  |  | Do not assemble
31 | 1 | AUX-4 | Header 18 Positions | 18 POS | Pitch 0.1"/Contact length 5.8mm/18 Pos/1 Row | MPE Connector | 087-1-018-0-F-XS0-1080 |  |  | Do not assemble
32 | 5 | - | Long Header 8 Positions | 8 POS | Pitch 0.1"/Contact length 15.8mm/8 Pos/1 Row | MPE Connector | 087-1-008-0-F-XS0-2160 |  |  | Do not assemble
33 | 1 | - | Long Header 6 Positions | 6 POS | Pitch 0.1"/Contact length 15.8mm/6 Pos/1 Row | MPE Connector | 087-1-006-0-F-XS0-2160 |  |  | Do not assemble
34 | 2 | - | Long Header 18 Positions | 18 POS | Pitch 0.1"/Contact length 15.8mm/18 Pos/1 Row | MPE Connector | 087-1-018-0-F-XS0-2160 |  |  | Do not assemble

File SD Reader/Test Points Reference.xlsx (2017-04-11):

Test Points Signals
# TEST POINT | SIGNAL | DESCRIPTION
TP1 | 5V | 5V Input voltage
TP2 | 3,3V | 3,3V LDO Output voltage
TP3 | DI | Data IN (MOSI)
TP4 | CLK | Clock Signal
TP5 | CS | Chip Select
TP6 | DO | Data OUT (MISO)
TP7 | CD | Card Detection
TP8 | GND | Ground Reference

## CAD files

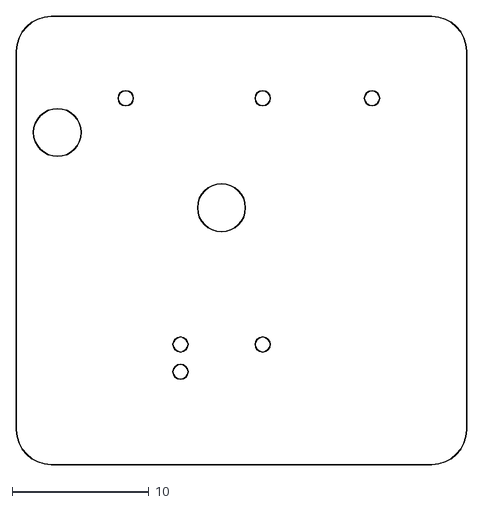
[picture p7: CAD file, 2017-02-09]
Extruder Board/ATE/Smart Extruder Board.dxf
32.9 x 32.8

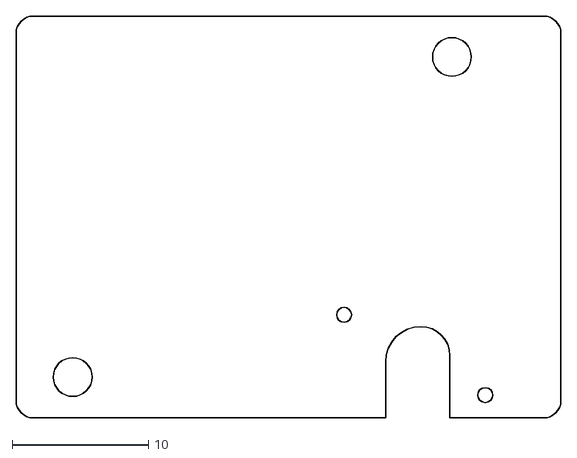
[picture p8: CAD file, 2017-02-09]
Silent Stepper Driver 4L/ATE/Silent Stepper Driver Callibration plate.dxf
40.0 x 29.5

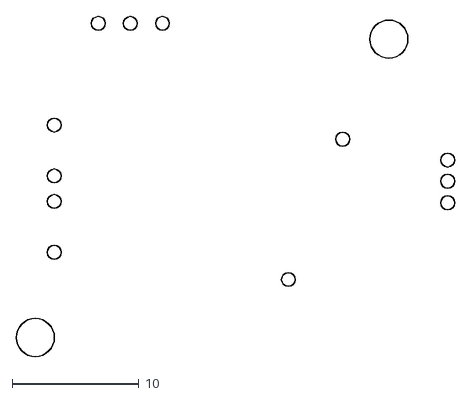
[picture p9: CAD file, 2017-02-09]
Silent Stepper Driver 4L/ATE/Silent Stepper Driver bottom plate.dxf
34.5 x 26.8

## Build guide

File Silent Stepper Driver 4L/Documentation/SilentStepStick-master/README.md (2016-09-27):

# SilentStepStick
The Silent-Step-Stick is a Stepper Motor Driver Board based on a [Trinamic TMC 2100](http://www.trinamic.com/products/integrated-circuits/stepper-power-driver/tmc2100) or [Trinamic TMC 2130](http://www.trinamic.com/products/integrated-circuits/stepper-power-driver/tmc2130).
The driver boards are hardware compatible with [StepStick](http://reprap.org/wiki/StepStick) and [Pololu A4988](https://www.pololu.com/product/1182).

SilentStepStick (http://www.watterott.com/en/SilentStepStick)

## Shop
* Trinamic **TMC2100** based drivers (CFG pins for configuration)
  * [TMC2100 SilentStepStick (3.3-5V)](http://www.watterott.com/en/SilentStepStick)
  * [TMC2100 SilentStepStick (3.3-5V) with soldered Pin Headers](http://www.watterott.com/en/SilentStepStick-with-Pins)
* Trinamic **TMC2130** based drivers (SPI for configuration)
  * [TMC2130 SilentStepStick (3.3-5V)](http://www.watterott.com/en/SilentStepStick-TMC2130)
  * [TMC2130 SilentStepStick (3.3-5V) with soldered Pin Headers](http://www.watterott.com/en/SilentStepStick-TMC2130-with-Pins)
* Accessories
  * [SilentStepStick Protector (with flyback diodes)](http://www.watterott.com/en/SilentStepStick-Protector)
  * [Suitable Heatsink 10x10mm](http://www.watterott.com/en/Pin-heatsink-square-ICK-S-10-x-10-x-125)
  * [Suitable Heatsink 10x6mm](http://www.watterott.com/en/Heatsink-for-DIL-IC-PLCC-und-SMD-10-x-6-mm)

## Features
* Hardware compatible with [StepStick](http://reprap.org/wiki/StepStick) and [Pololu A4988](https://www.pololu.com/product/1182)
* Trinamic TMC21x0 stepper motor driver
* Step/Dir interface with up to 16 microsteps and 256 microsteps interpolation
* Motor current: up to **1.2A RMS** continuously and 2.5A short time peak current per coil
* Motor voltage: **5.5...45V**
* **microPlyer** - microstep interpolator for increased smoothness of microstepping
* **stealthChop** - for quiet operation and smooth motion
* **spreadCycle** - highly dynamic motor control chopper
* Extra features of **TMC2130**:
  * SPI configuration interface (up to 4MHz)
  * up to 256 native microsteps (without interpolation)
  * **coolStep** - current control for energy savings
  * **stallGuard** - sensorless motor load detection
  * **dcStep** - load dependent speed control

## Hardware
* [Schematics/Layout + Guide](https://github.com/watterott/SilentStepStick/tree/master/hardware)
* [FAQ (Frequently Asked Questions)](https://github.com/watterott/SilentStepStick/blob/master/docu/FAQ.md)
* [Eagle CAD Part](https://github.com/watterott/Eagle-Libs)

## Reviews and Tests

* Review from Thomas Sanladerer:

  SilentStepStick/TMC2100 Review (https://www.youtube.com/watch?v=g6Bxoqr8QlY)

  SilentStepStick/TMC2100 Review Update (https://www.youtube.com/watch?v=mYuZqx8xwTg)

* Review from Peter Recktenwald:

  SilentStepStick/TMC2100 Review (https://www.youtube.com/watch?v=P3ebhi-vZRY)

* Review from Georg Mill:

  [](http://blog.georgmill.de/2015/06/18/schrittmotor-test-5-treiber-im-vergleich/)

* What is Trinamic stallGuard2 and coolStep:

  Trinamic stallGuard2 and coolStep (https://www.youtube.com/watch?v=Prw7wNa20Gk)

* Tests:
  * [Watterott (Stepper Motor)](https://www.youtube.com/watch?v=0l-HlntFYOY)
  * [Aleks (RepRap Prusa i3)](https://www.youtube.com/watch?v=33jQ0P7SMJA)
  * [Anthony (Delta Printer)](https://www.youtube.com/watch?v=CZOV0BdgSiU)
  * [Mario Lukas](https://www.youtube.com/watch?v=mJmg0iRHX8s)
  * Yusuke Sasaki: [TMC2100 steahlChop](https://www.youtube.com/watch?v=wrS7l46YJ_E), [TMC2100 spreadCycle](https://www.youtube.com/watch?v=391TY72wzPQ), [A4988](https://www.youtube.com/watch?v=iw6MRjzS6V4)
  * [MakerSpatz (Ultimaker)](https://www.youtube.com/watch?v=0jPbzB7XtWg)
  * [Aitor Esteve Alvarado (Ninja Prusa i3)](https://www.youtube.com/watch?v=c_TCVirnKJ0)
  * [Artur Wronowski (Delta Printer)](https://www.youtube.com/watch?v=hH2UkAmbfYs)
  * [3D Huynh (Felix 3D)](https://www.youtube.com/watch?v=EglFOpTXPtg)
  * [Easy 3D (Sparkcube)](https://www.youtube.com/watch?v=BxE_F8_Ec8M)
  * [WOLF HSW (linear drive)](https://www.youtube.com/watch?v=wjuAu0WYOPM)
  * Clarence Lee (ATOM Delta Printer): [TMC2100](https://www.youtube.com/watch?v=sBVNqFybUZI), [DRV8825](https://www.youtube.com/watch?v=tNufJnybsxg), [A4982](https://www.youtube.com/watch?v=r1noUt2UoO8)
  * Alex Tien (3DP Delta Printer): [TMC2100](https://www.youtube.com/watch?v=RcqnXXp4tPA), [A4988](https://www.youtube.com/watch?v=F2oB_NOLxHU)
  * swdjojo (Prusa i3): [TMC2100](https://www.youtube.com/watch?v=vBRNifmHaZE), [A4988](https://www.youtube.com/watch?v=TCgErVx93OA)
  * [Doc. Snuggles (Stepper Motor)](https://www.youtube.com/watch?v=gj6f6HSrHc4)
  * [Robert Sertic (Ultimaker)](https://www.youtube.com/watch?v=1wQJZb0gzoE)
  * [Emanuel Kant (Ultimaker)](https://www.youtube.com/watch?v=Y7CG43yf9zA)
  * [ghicione (EggBot)](https://www.youtube.com/watch?v=4FBAAQXnESU)
  * Edward Kuo: [E3D Cyclops Delta Printer](https://www.youtube.com/watch?v=iEYdrMH69oo), [TMC2100 water cooled](https://www.youtube.com/watch?v=vjNM9R0NZG0)
  * [Noah Ahmad Connor (Prusa i3)](https://www.youtube.com/watch?v=mNdl3s8TYmY)
  * [Sterillium (XYZ DaVinci)](https://www.youtube.com/watch?v=k-szP5wuplM)
  * [markg21405 (Delta Printer)](https://www.youtube.com/watch?v=tytL3KeIlLw)
  * [JJiG (MakerFarm Pegasus)](https://www.youtube.com/watch?v=9Rny6n1MCfI)
  * [René Jurack (Skimmy v3)](https://www.youtube.com/watch?v=qpl8v0k1_34)

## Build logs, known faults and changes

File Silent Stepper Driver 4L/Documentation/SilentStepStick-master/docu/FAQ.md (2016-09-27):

# Frequently Asked Questions

## Is the SilentStepStick 100% compatible with a StepStick or Pololu A4988?
The SilentStepStick is hardware/pin compatible with StepStick and Pololu A4988 drivers.
However the TMC2100 has different and more settings, which can be set via the CFG/MS pins.
The TMC2100 config pins also know three states: low (GND), high (VIO) and open (unconnected).
On the TMC2130 SPI is used for the configuration and so the controller board must have SPI on the CFG pins.

## Where can I find more information on the settings and operation modes?
More information can be found in the [SilentStepStick schematics](https://github.com/watterott/SilentStepStick/tree/master/hardware) and [TMC2100 datasheet](http://www.trinamic.com/products/integrated-circuits/stepper-power-driver/tmc2100) / [TMC2130 datasheet](http://www.trinamic.com/products/integrated-circuits/stepper-power-driver/tmc2130).
For most cases the **1/16 stealthChop** mode (CFG1=open, CFG2=open, CFG3=open) is suitable.
If you have problems like step losses then use the more powerful **1/16 spreadCycle** mode (CFG1=GND, CFG2=open, CFG3=open).

#### Installation Guides for 3D Printers
* [General (English)](http://reprap.org/wiki/TMC2100)
* [General (German)](http://reprap.org/wiki/TMC2100/de)
* [General (Russian)](http://3deshnik.ru/blogs/akdzg/chto-zhe-delat-belami-tmc2100)
* [RAMPS (English)](http://www.instructables.com/id/Install-and-configure-SilentStepStick-in-RAMPS-TMC/)
* [Ultimaker UMO + TMC2100 (English)](https://ultimaker.com/en/community/11571-step-by-step-installation-of-silentstepstick-drivers-on-umo)
* [Ultimaker UMO + TMC2130 (English)](https://ultimaker.com/en/community/20090-step-by-step-installation-of-sss-tmc2130-on-umo)

#### Boards with USB Power Supply
If you use a control board with USB power supply (like Arduino + RAMPS) then always ensure that ```VM``` is present, when you connect the board via USB.
Otherwise the TMC21x0 is not powered via the internal voltage regulator and a high current can flow into ```VIO``` and this can damage the internal logic.
As safety workaround you can disconnect the 5V signal in the USB cable, so that the board cannot be powered over USB.

#### RAMPS 1.4 and RUMBA Notes
If you remove all jumpers (or open all switches) for MS1+MS2+MS3, then the SilentStepStick TMC2100 driver will be in 1/16 spreadCycle mode (CFG1=GND, CFG2=open, CFG3=open), because there is a pull-down resistor on MS1 on the RAMPS.
But if you have not an original [RAMPS 1.4](http://reprap.org/wiki/RAMPS_1.4) or [RUMBA](http://reprap.org/wiki/RUMBA), then your schematics can be different and you have to check the MS-Pin configurations on you board.

## How to set the stepper motor current?
The best way to set the motor current is by measuring the voltage on the ```Vref``` pin (0...2.5V) and
adjusting the voltage with the potentiometer.
The maximum motor current is 1.77A RMS and is set via the 0.11Ohm sense resistors.

```Irms = (Vref * 1.77A) / 2.5V = Vref * 0.71```

```Vref = (Irms * 2.5V) / 1.77A = Irms * 1.41```

**Example:** A voltage of 1.0V on Vref sets the motor current to 0.71A RMS.

**Note:** On some stepper motor drivers the maximum current (e.g. A4988) is set via Vref and on others the RMS current (e.g. TMC2100).
          ```Imax = 1.41 * Irms```

## What to consider when turning the power supply on or off?
**Power on:**
The motor supply voltage ```VM``` should come up first and then ```VIO```, because the internal logic of the TMC21x0 driver is powered from ```VM```.
If you cannot ensure that ```VM``` is present before or at the same time as ```VIO``` then add a resistor with about 100-200 Ohm in series with ```VIO``` to protect the internal logic.
Only after ```VIO``` is present and stable, the driver inputs (STEP, DIR, EN, CFG1...) can be driven with a high level.

**Power off:**
If the motor is running/moving, then it is not allowed to switch off the power supply. Always make sure that the motor stands still on shutting down otherwise the TMC21x0 driver can get damaged.
An **emergency stop** can be realized, when the ```EN/CFG6``` pin is set to ```VIO```. This will switch off all power drivers and will put the motor into freewheeling.
See also: [SilentStepStick Protector with flyback diodes](https://github.com/watterott/SilentStepStick#shop)

## The motor makes noise in spreadCycle mode when it is not moving?
A motor supply voltage of 12V is in most cases to low and in general the sound gets quieter if the motor supply voltage is above 18V.

## How to control the TMC21x0 stepper motor driver?
The SilentStepStick has a normal step+direction interface.
You set the direction with the ```DIR``` pin and on every pulse on the ```STEP``` pin the motor will move one step.
Here you can find an [Arduino example](https://github.com/watterott/SilentStepStick/tree/master/software) and [Arduino library](http://www.airspayce.com/mikem/arduino/AccelStepper/) (interface=DRIVER).

## Is it possible to connect the CFG pins from different SilentStepSticks?
It is possible to connect the ```CFG``` pins from two or more driver boards.
However then the pin state can only be ```GND``` (low) or ```VIO``` (high). The open state (unconnected) is not possible in this configuration.

## Why is the TMC2100 chip on the bottom PCB side?
The TMC2100/TMC2130 chip has a thermal pad on the bottom which is soldered to the PCB.
So the thermal resistance via the chip bottom is better than via the top.
That is why the chip is on the bottom PCB side.
A heat sink can be placed directly on the PCB.
Further infos [here](https://www.youtube.com/watch?time_continue=145&v=mYuZqx8xwTg).

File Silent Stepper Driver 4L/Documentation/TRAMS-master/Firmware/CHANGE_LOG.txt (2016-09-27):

V0.91:
-Cleaned up, removed comments and unused lines
-TRAMS has its own board configuration
-Homing uses defines from Configuration.h

V0.92:
-Smoother circles and corners

V0.93
-StallGuard2 added. ATTENTION: still in beta phase
-In configuration.h you can now choose the homing direction and the homing switch (left/right)

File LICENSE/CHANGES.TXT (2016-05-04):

This file will hold all the changes made by the Licensees.

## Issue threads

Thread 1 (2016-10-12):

Driver for mac

Zorgonaute84, 2016-10-12:
Hello,

The Sigma is not recognized by Cura with a Mac. Is it possible to provide us the driver ?

The Arduino clone used for the Sigma looks don't use the same driver as the original. It's a real problem for Mac user who they don't have a Windows computer.

Thanks

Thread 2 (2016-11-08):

Update for existing client

Zorgonaute84, 2016-11-08:
I have a question, is it schedule to upgrade some parts of the first client's Sigma ? I think mainly of the Stepper driver board.

It could be a good and very positive attitude when we think that your firsts customers was considered like beta customer.

kitusmark, 2016-11-09:
Hi @Zorgonaute84

We're currently implementing in the production chain the new improvements made this year. As far I know, the different upgrades will be available soon to buy. About the pre-series printers I have no idea. Better if you send an email to info@bcn3dtechnologies.com.

Zorgonaute84, 2016-12-17:
Here we are... My left extruder's stepper driver was gone for the 2nd time...
I ask you again about the new Stepper driver, is it possible to replace my old out of service stepper driver by the new version ? Is it possible to change the both (left and right) at the same time ?

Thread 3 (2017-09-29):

X & Y-axis stepper driver board resistive setup

JosselinCLEMENT, 2017-09-29:
Hi Team,

Could you please let me know what are the original resistive setup of the X & Y stepper driver boards?

I tested the X axis resistivity and it was about 5 kOhm (ground to phase):

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

I am facing big issues with Y-axis shifting and I think that is mainly due to the Y-axis stepper board resistance setup.

Could you please update me?

Thank you very much for your support.

Joss

WanaGo, 2017-10-14:
Is this helpful?
[Driver-voltage.pdf](https://github.com/BCN3D/BCN3DSigma-Electronics/files/1384472/Driver-voltage.pdf)

JosselinCLEMENT, 2017-10-26:
Hi WanaGo,

Thank you very much for your support! It works :+1: !

Closed 2017-10-26.

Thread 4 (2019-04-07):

Updated Files

WanaGo, 2019-04-07:
Hello,
When will BCN3D update the Electronics, CAD files and BOM files to suit the current printers? These have not changed for quite a few years. When I got my printer a few years ago, it was not up to date then and it still has not changed.
Please can you update these repositories with the current CAD and Electronics files?
Thanks

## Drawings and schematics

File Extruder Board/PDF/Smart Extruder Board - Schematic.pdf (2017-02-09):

## INPUT

A

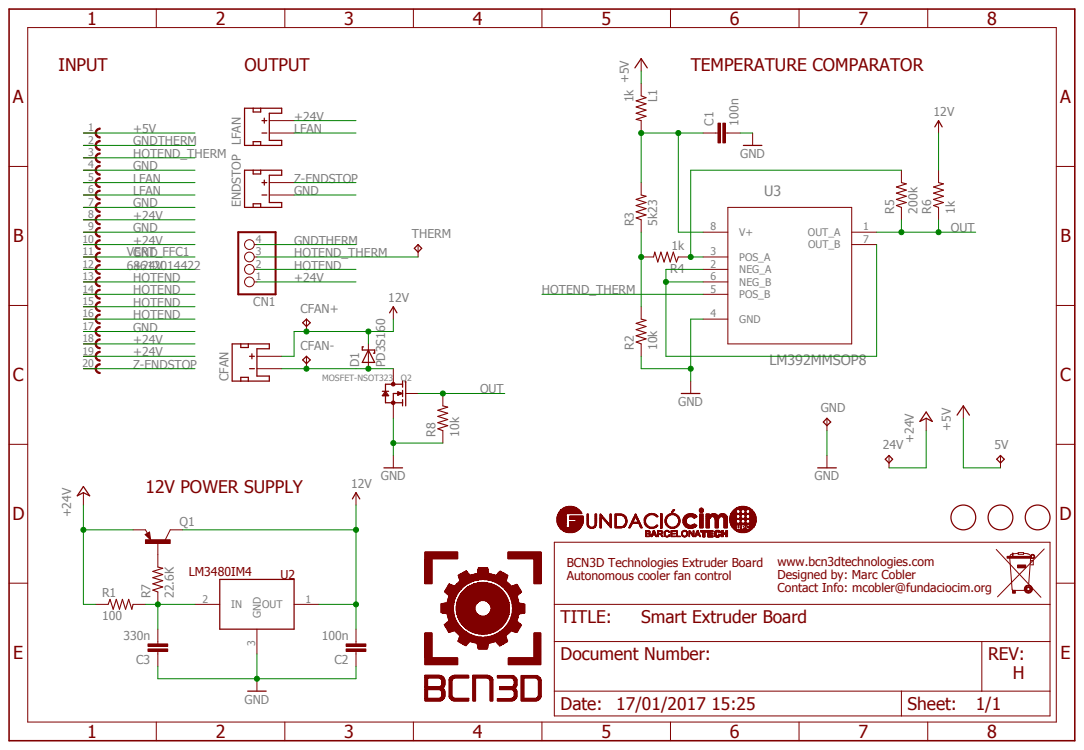
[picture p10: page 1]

GND

BCN3D Technologies Extruder Board
Autonomous cooler fan control

www.bcn3dtechnologies.com
Designed by: Marc Cobler
Contact Info: mcobler@fundaciocim.org

Document Number: | REV: H

Date: 17/01/2017 15:25 | Sheet: 1/1

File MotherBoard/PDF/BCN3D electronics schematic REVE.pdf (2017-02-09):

## BCN3D - Barcelona 2014 Marc Cobler Cosmen

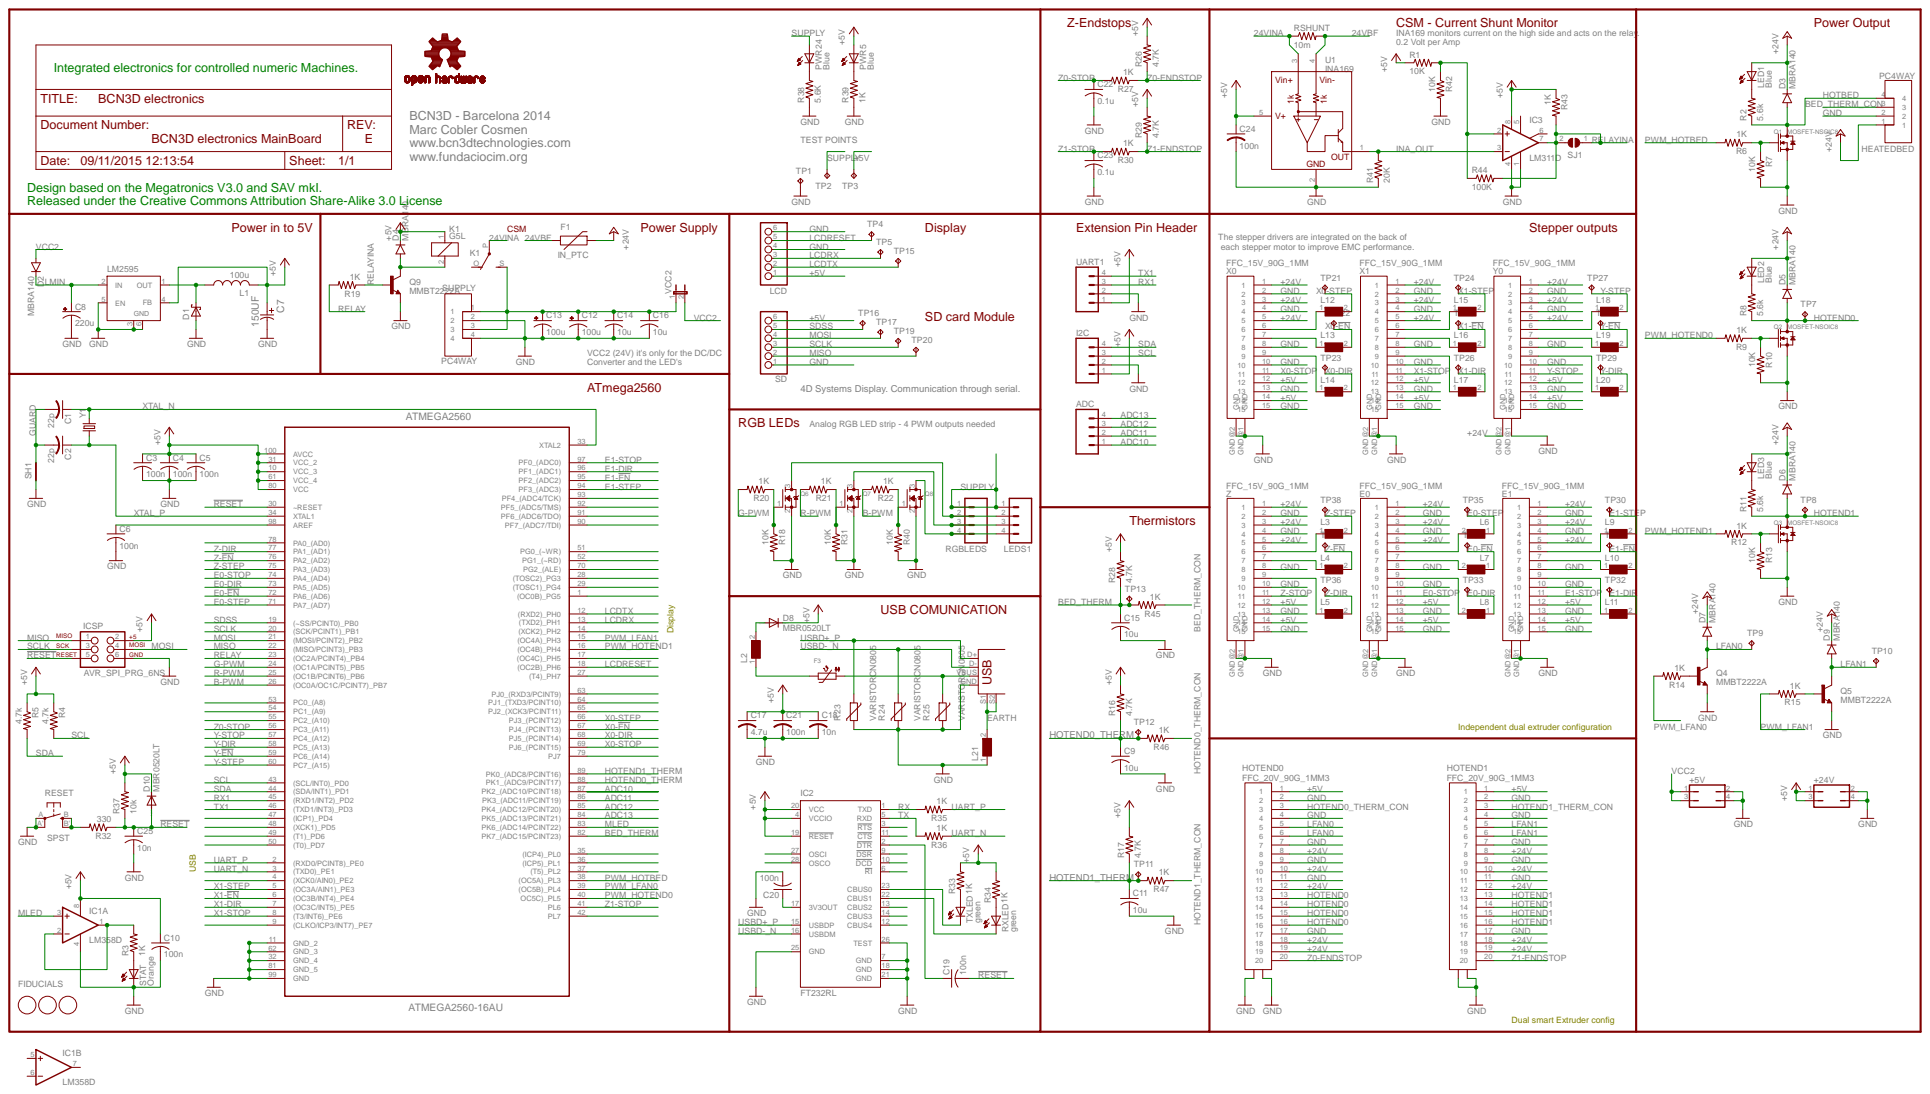
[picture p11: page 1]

INA169 monitors current on the high side and acts on the relay.
0.2 Volt per Amp

Integrated electronics for controlled numeric Machines.

Design based on the Megatronics V3.0 and SAV mkI.
Released under the Creative Commons Attribution Share-Alike 3.0 License

The stepper drivers are integrated on the back of
each stepper motor to improve EMC performance.

VCC2 (24V) it's only for the DC/DC
Converter and the LED's
ATmega2560

Analog RGB LED strip - 4 PWM outputs needed

Independent dual extruder configuration

Dual smart Extruder config

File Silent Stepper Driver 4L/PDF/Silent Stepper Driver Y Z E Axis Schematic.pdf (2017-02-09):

A

A

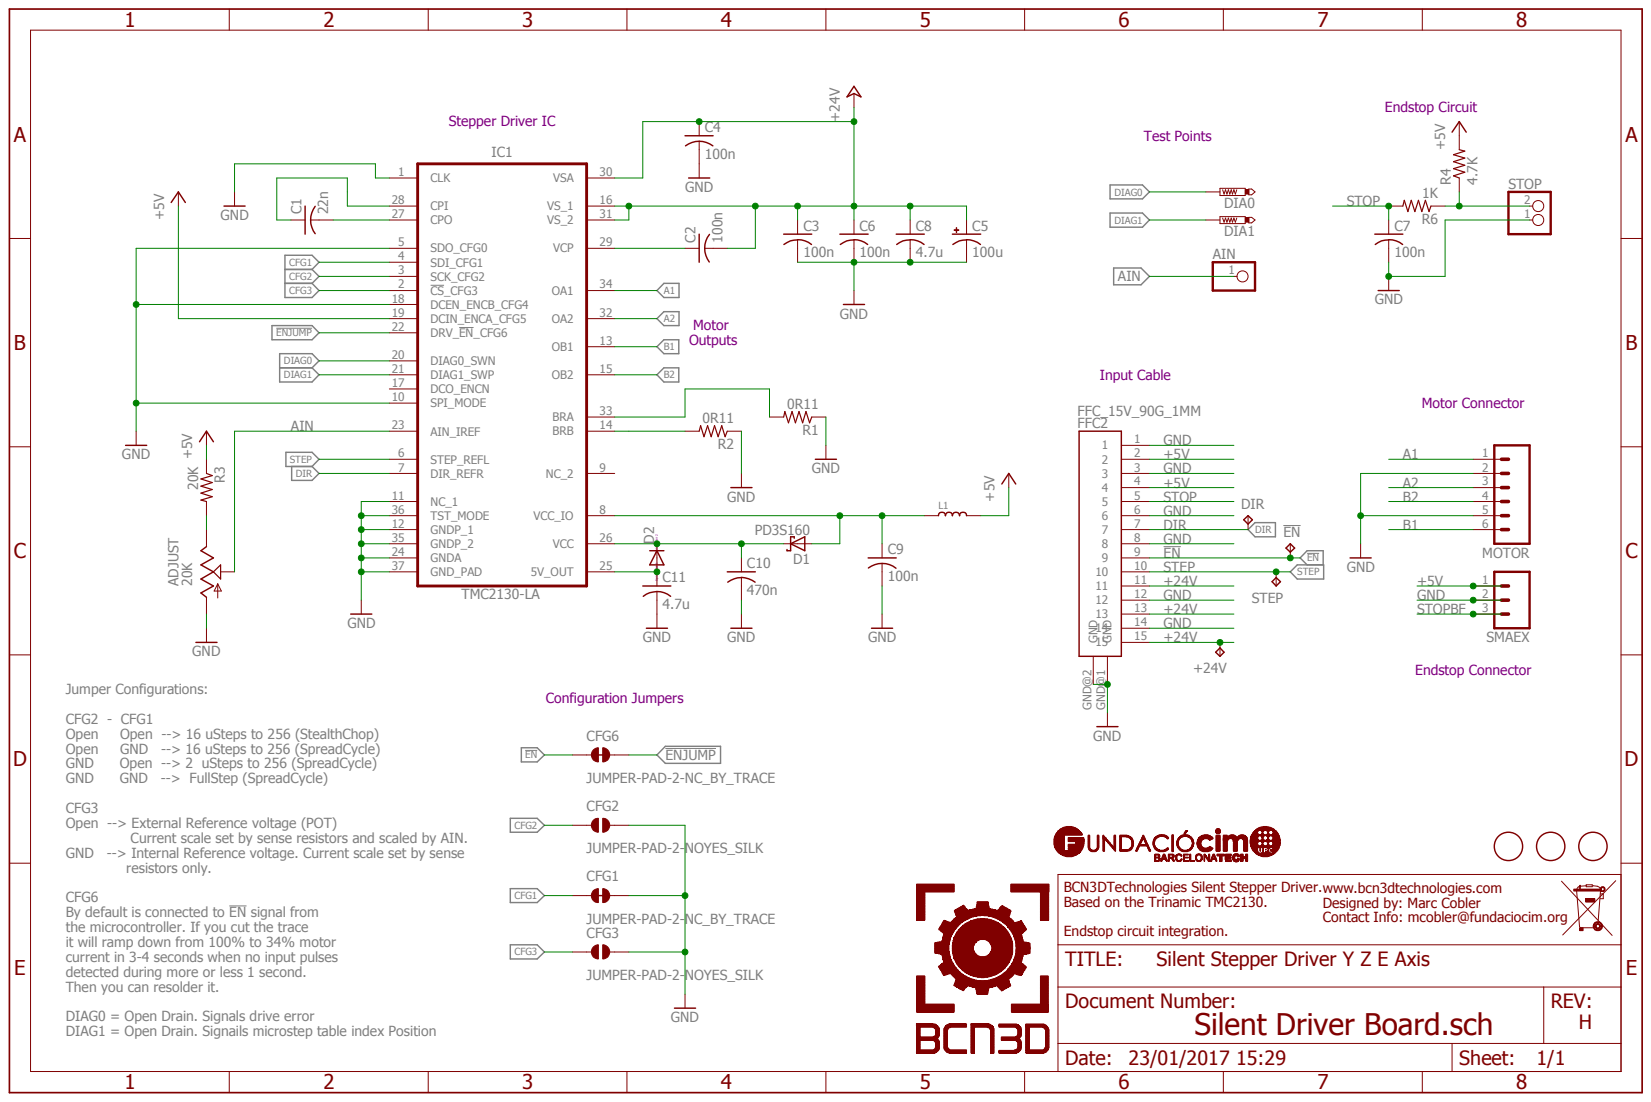
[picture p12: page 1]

CFG3
Open --> External Reference voltage (POT)

Current scale set by sense resistors and scaled by AIN.

GND --> Internal Reference voltage. Current scale set by sense

CFG6
By default is connected to EN signal from
the microcontroller. If you cut the trace
it will ramp down from 100% to 34% motor
current in 3-4 seconds when no input pulses

BCN3DTechnologies Silent Stepper Driver.
Based on the Trinamic TMC2130.

www.bcn3dtechnologies.com
Designed by: Marc Cobler
Contact Info: mcobler@fundaciocim.org

Silent Stepper Driver Y Z E Axis

detected during more or less 1 second.
Then you can resolder it.

Document Number: Silent Driver Board.sch | REV: H

DIAG0 = Open Drain. Signals drive error
DIAG1 = Open Drain. Signails microstep table index Position

Date: 23/01/2017 15:29 | Sheet: 1/1

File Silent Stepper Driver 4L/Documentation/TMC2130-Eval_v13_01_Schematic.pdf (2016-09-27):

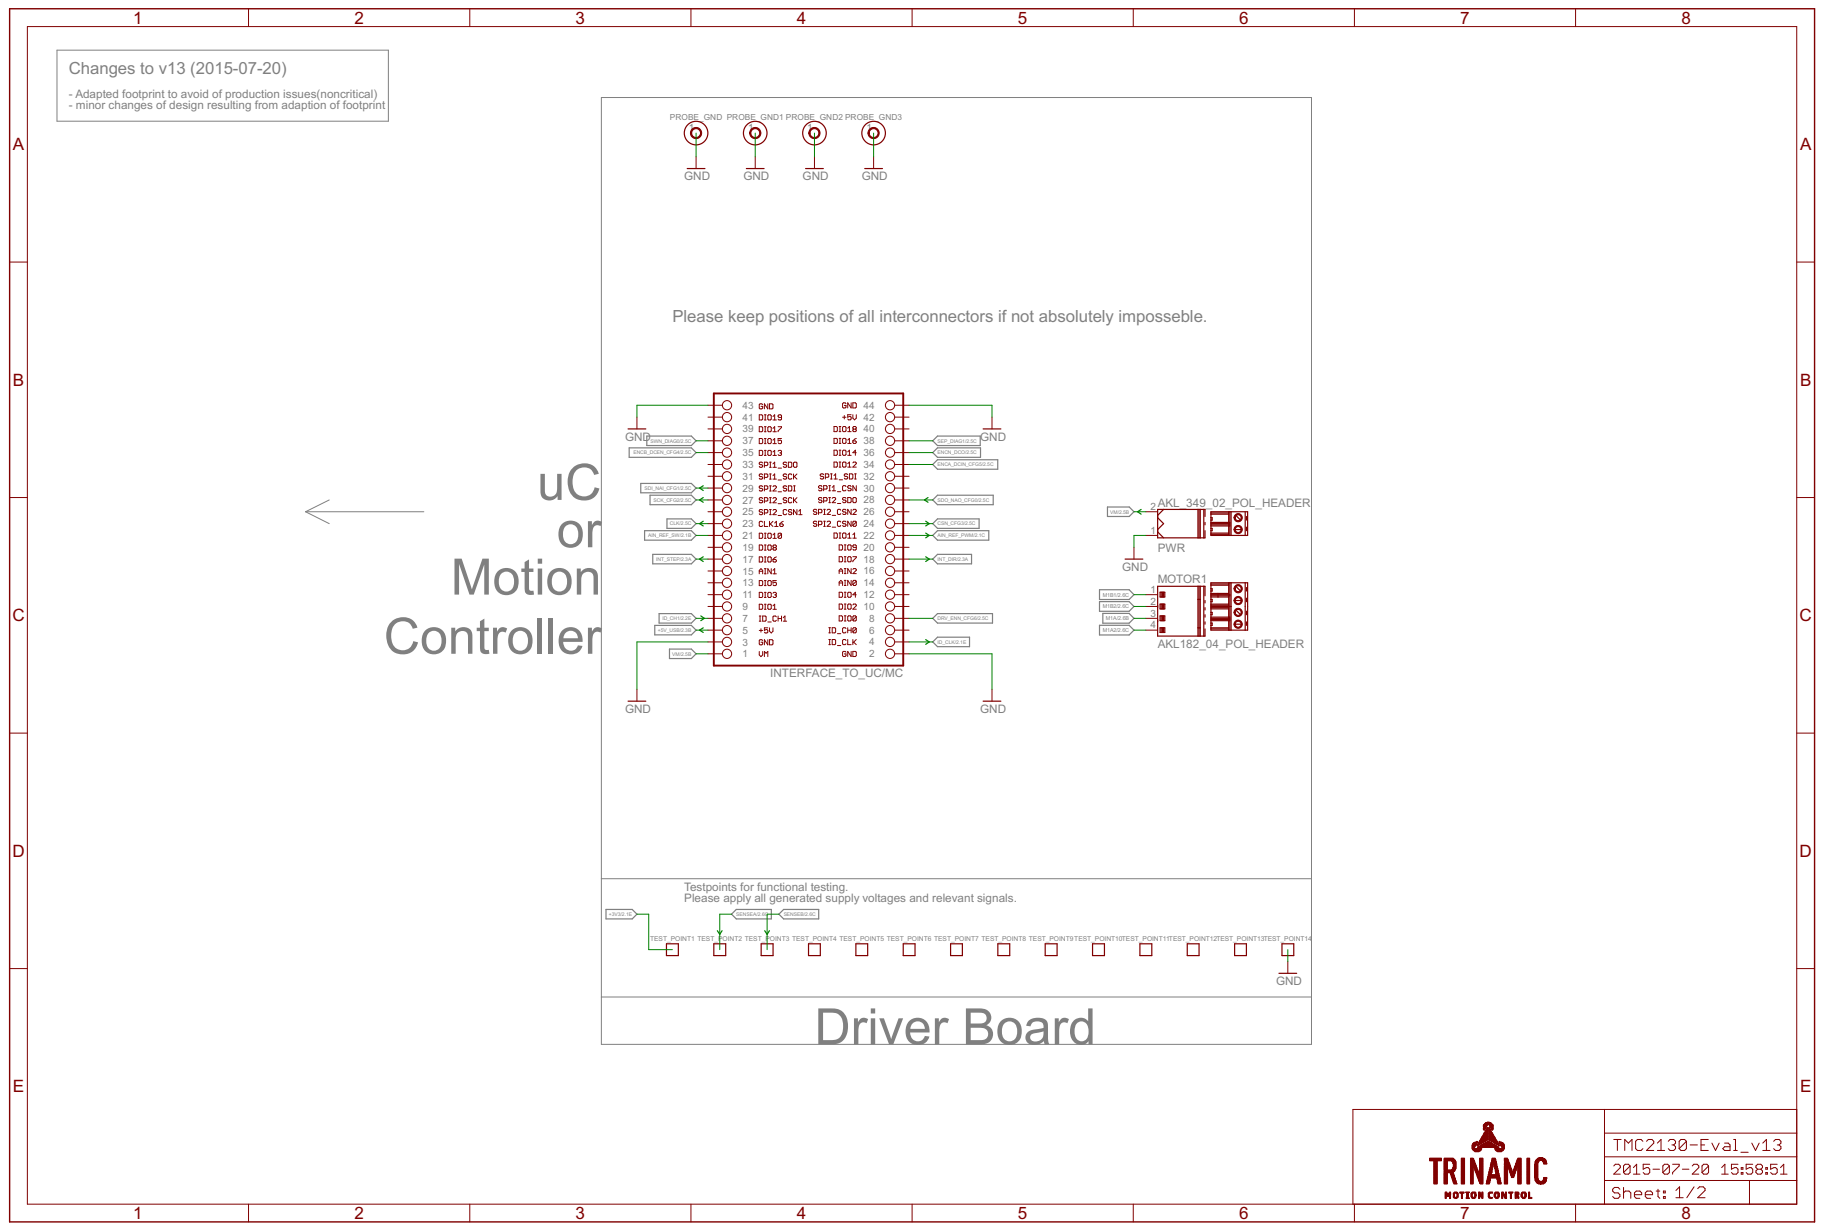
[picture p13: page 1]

- Adapted footprint to avoid of production issues(noncritical)
- minor changes of design resulting from adaption of footprint

Please keep positions of all interconnectors if not absolutely imposseble.

Testpoints for functional testing. Please apply all generated supply voltages and relevant signals.

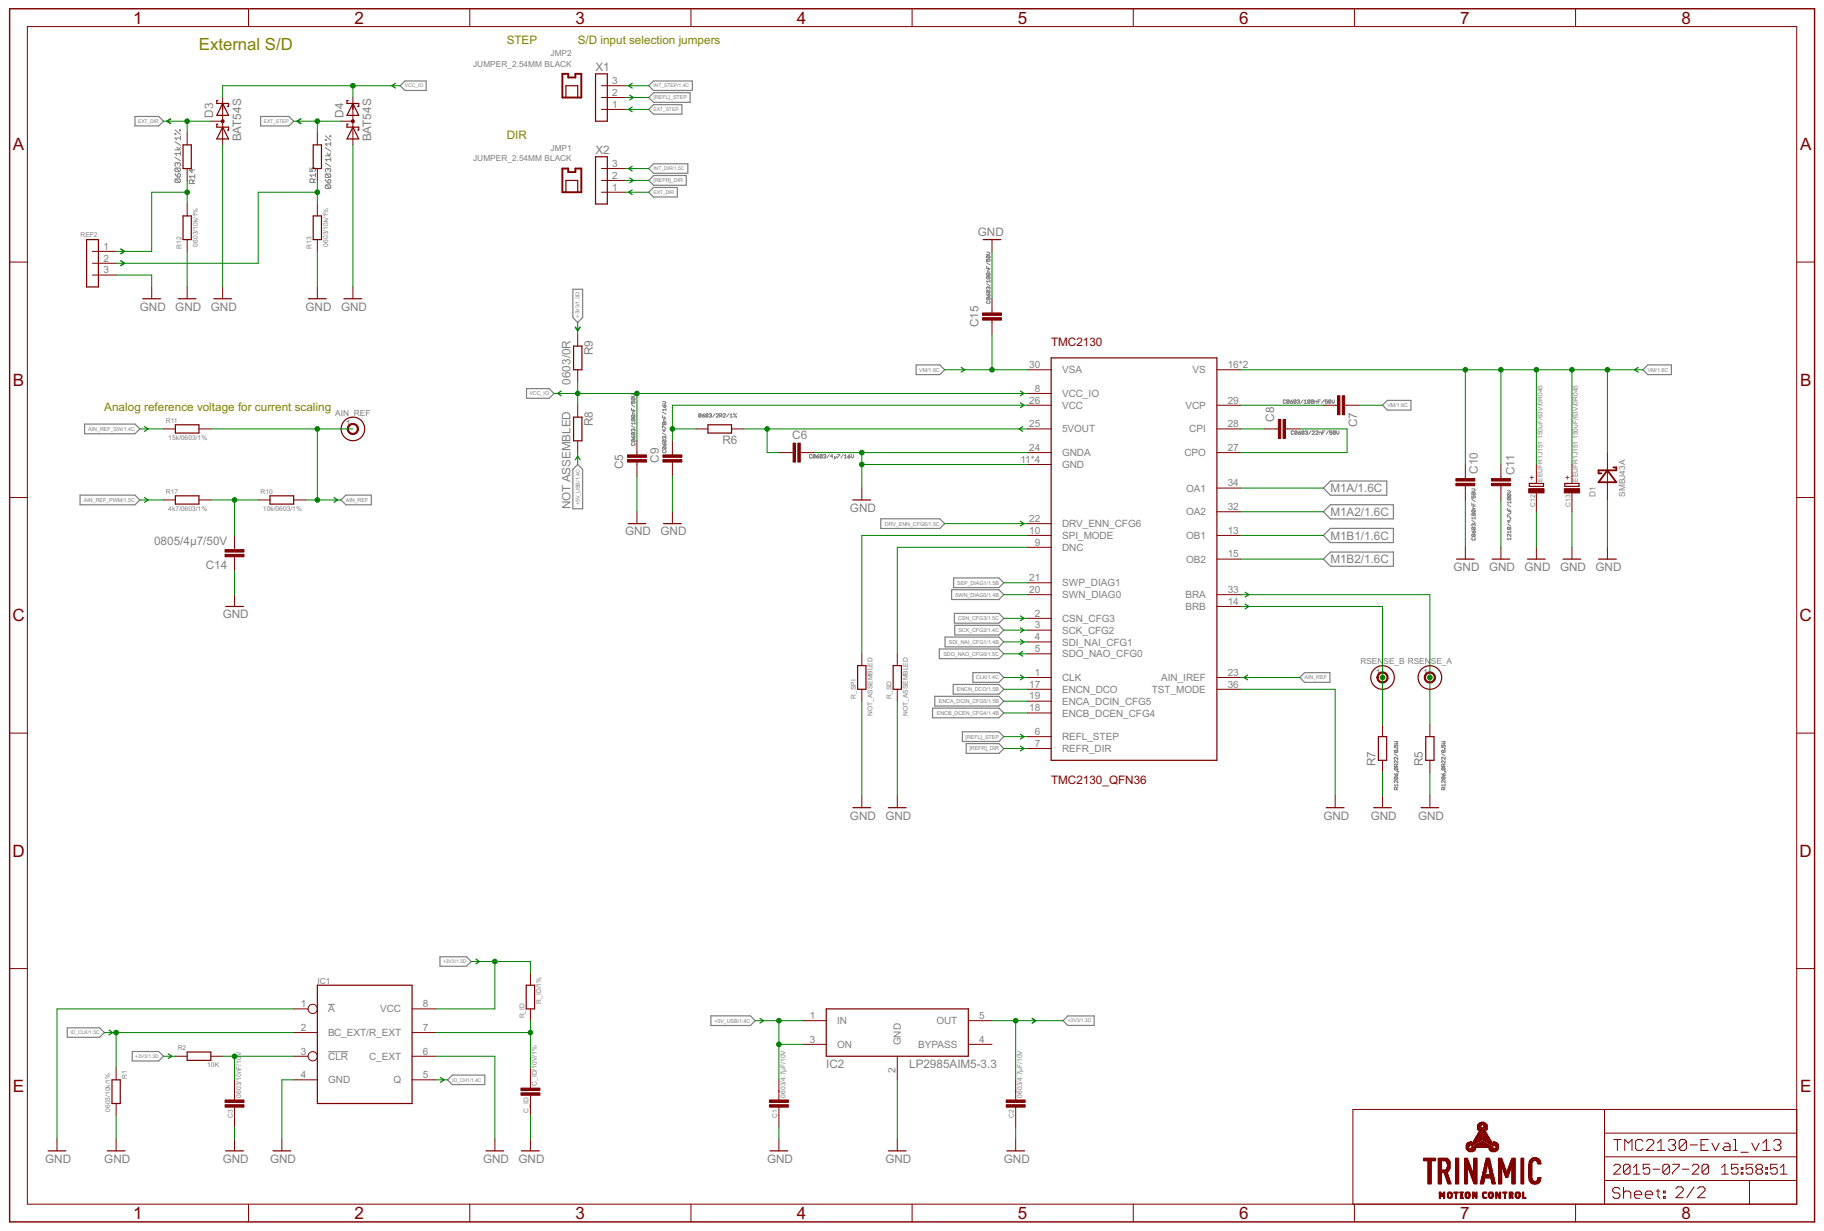
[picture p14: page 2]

External S/D

Analog reference voltage for current scaling

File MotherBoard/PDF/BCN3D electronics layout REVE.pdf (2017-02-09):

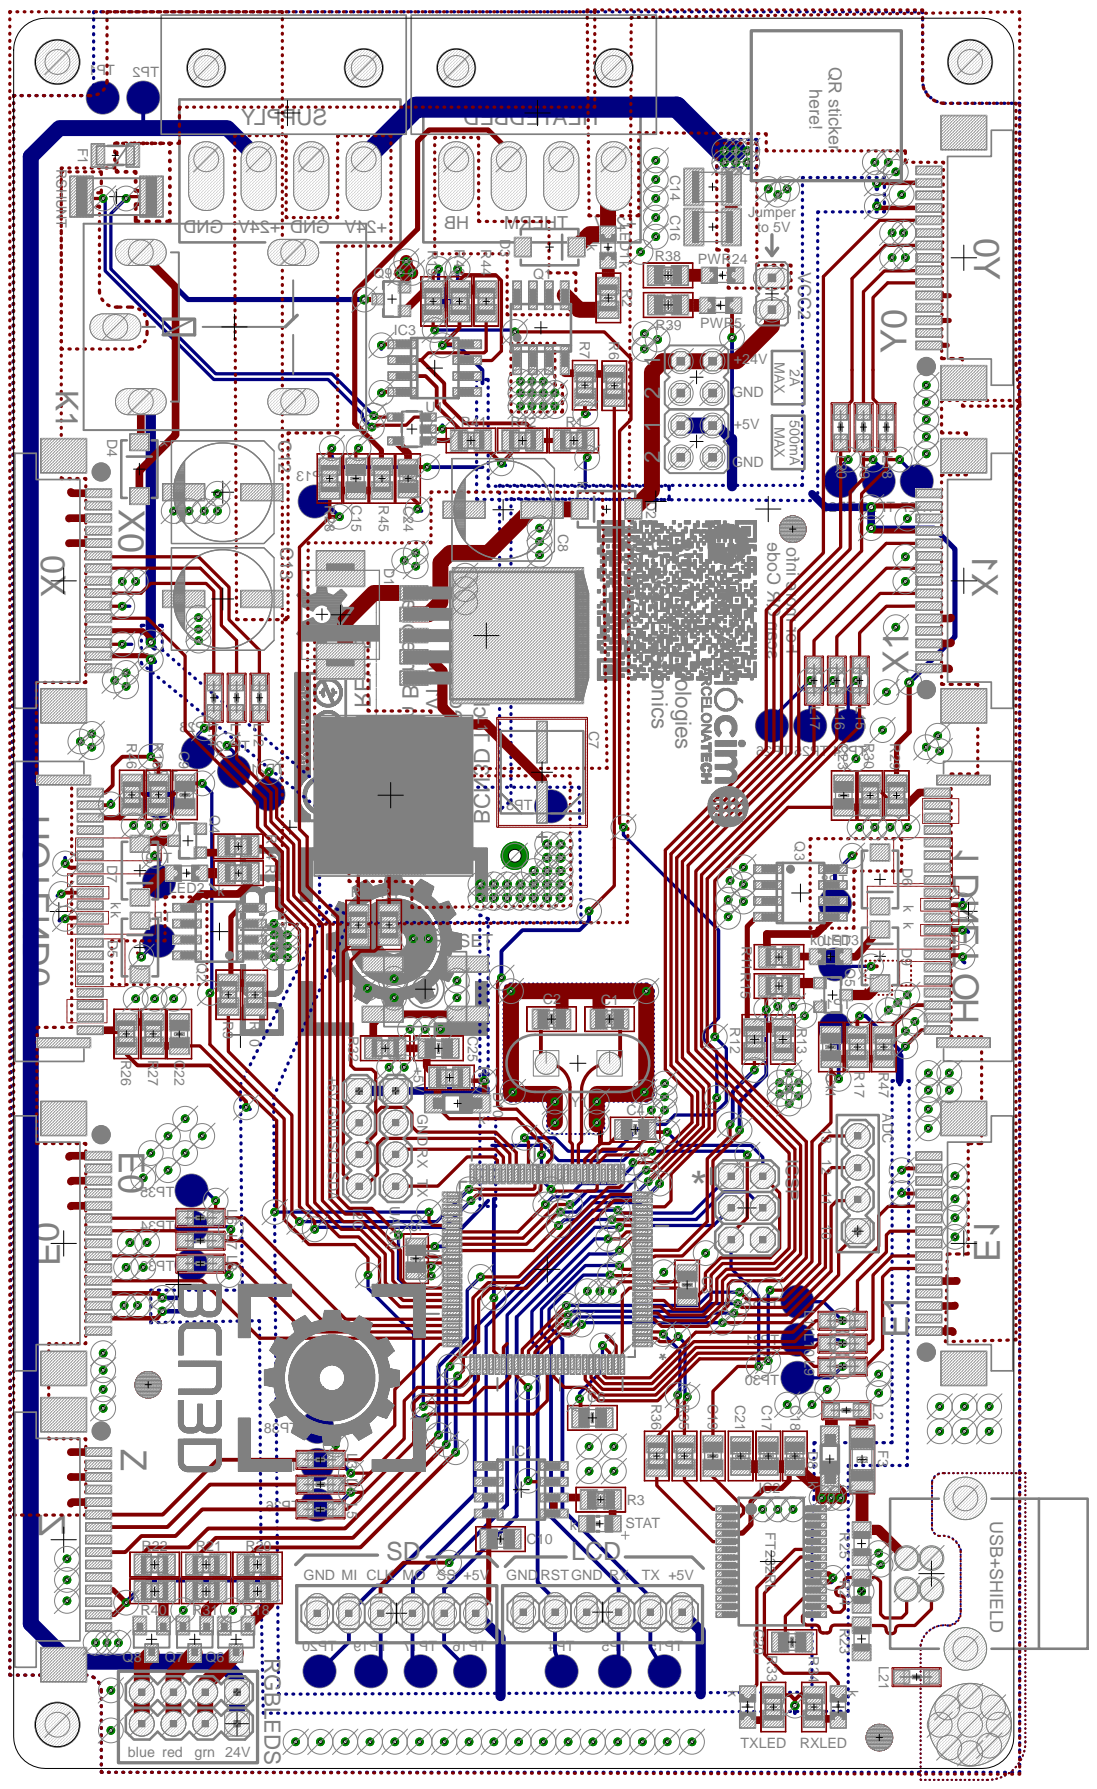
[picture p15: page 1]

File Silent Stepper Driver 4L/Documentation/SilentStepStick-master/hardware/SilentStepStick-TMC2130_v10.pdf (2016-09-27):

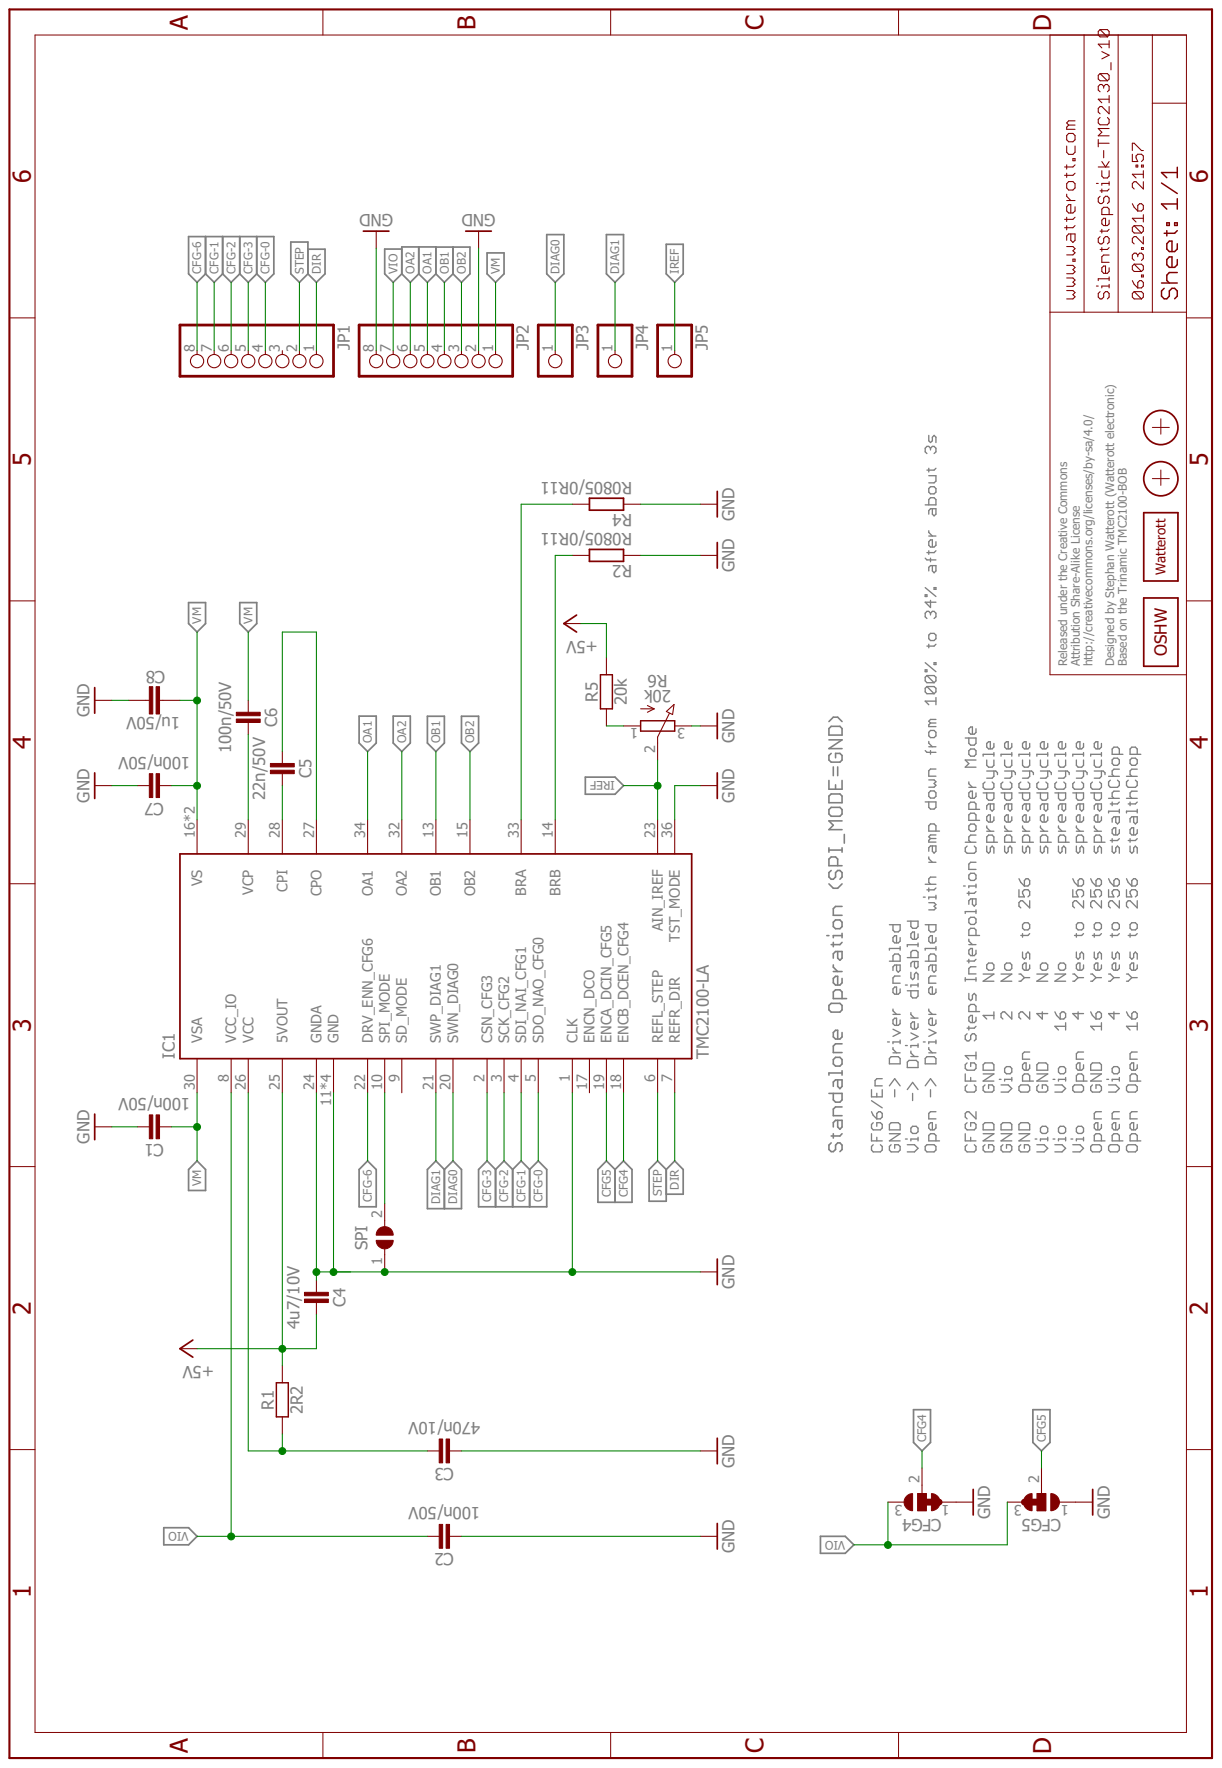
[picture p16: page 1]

Released under the Creative Commons Attribution Share-Alike License http://creativecommons.org/licenses/by-sa/4.0/ Designed by Stephan Watterott (Watterott electronic) Based on the Trinamic TMC2100-BOB

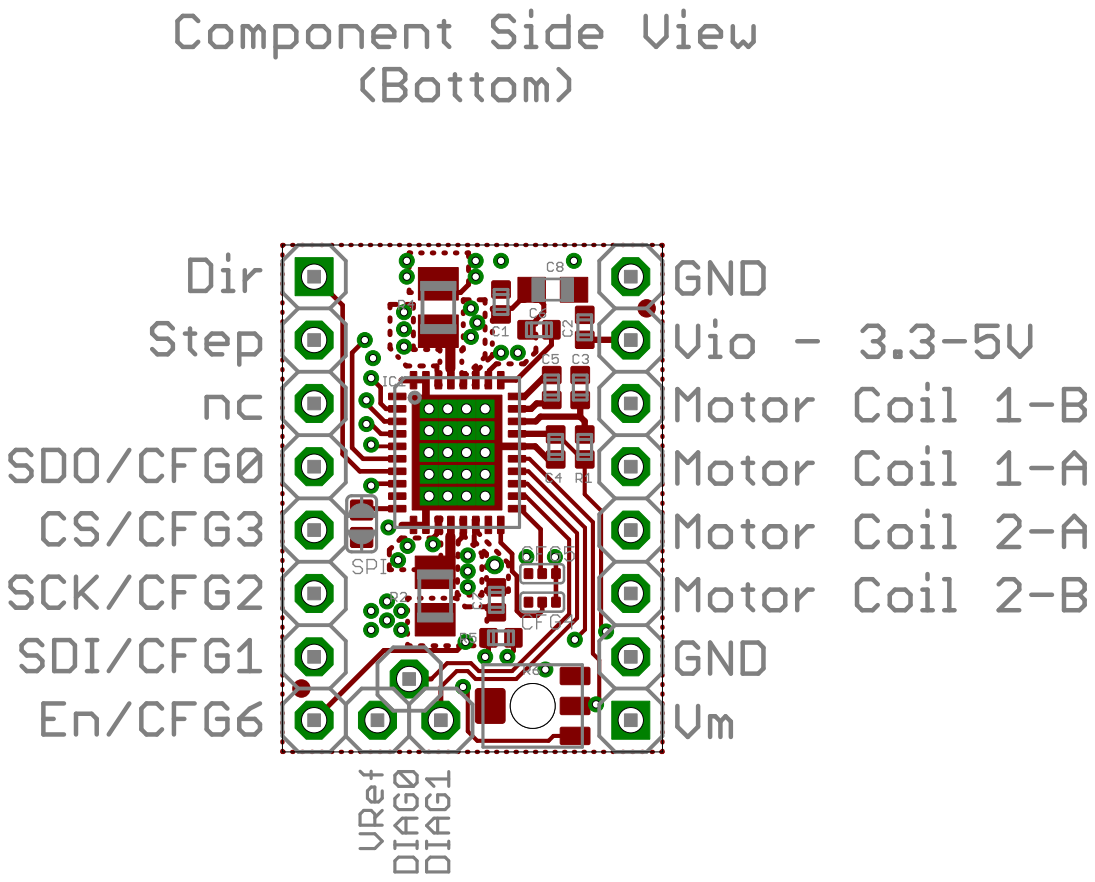
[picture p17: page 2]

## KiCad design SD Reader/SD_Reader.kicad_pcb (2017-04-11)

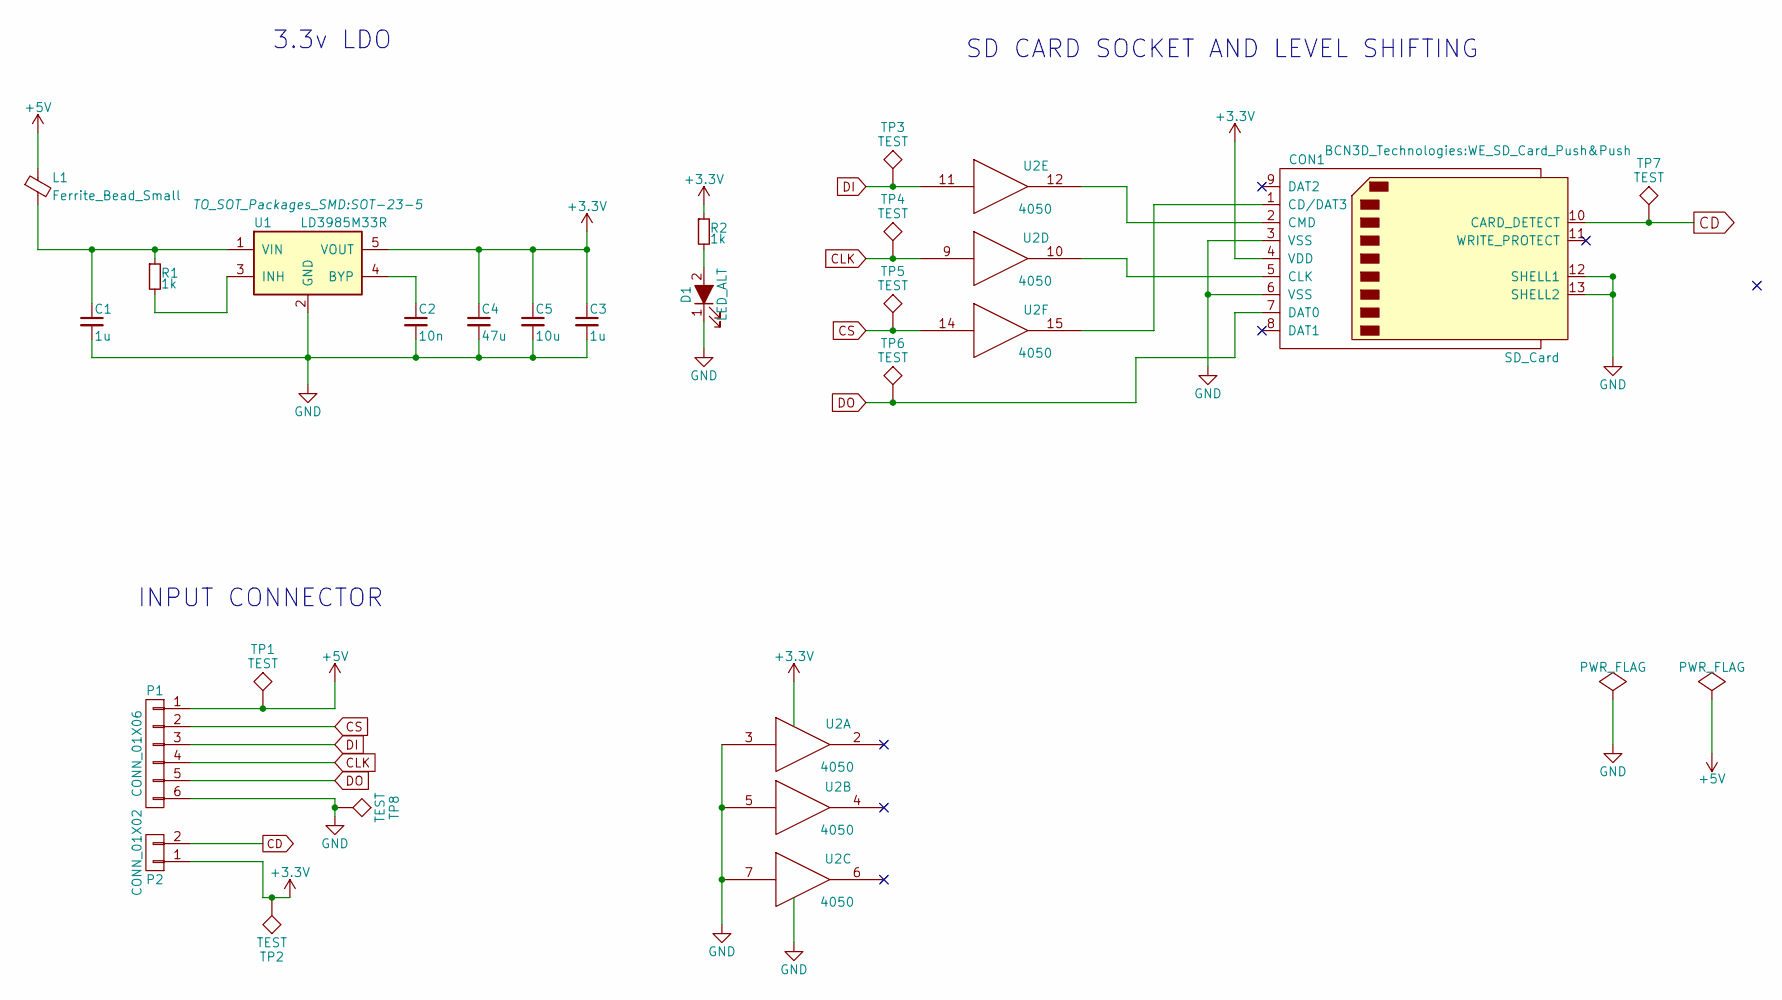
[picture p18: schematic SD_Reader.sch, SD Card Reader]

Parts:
C1, C3: 1u; C_0603
C2: 10n; C_0603
C4: 47u; C_1210
C5: 10u; C_0805
CON1: SD_Card; WE_SD_Card_Push&Push
D1: LED_ALT; LED_0603
L1: Ferrite_Bead_Small; R_0603
P1: CONN_01X06; Pin_Header_Straight_1x06_Pitch2.54mm_SMD_Pin1Right
P2: CONN_01X02; Pin_Header_Straight_1x02_Pitch2.54mm
R1, R2: 1k; R_0603
TP1, TP2, TP3, TP4, TP5, TP6, TP7, TP8: TEST; Measurement_Point_Round-SMD-Pad_Small
U1: LD3985M33R; SOT-23-5
U2: 4050; SO-16-N

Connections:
+3V3: C3.1, C4.1, C5.1, CON1.4 (VDD), P2.1, R2.1, TP2.1, U1.5 (VOUT), U2.1 (VCC)
+5V: L1.1, P1.1, TP1.1
CD: CON1.10 (CARD_DETECT), P2.2, TP7.1
CLK: P1.4, TP4.1, U2.9
CS: P1.2, TP5.1, U2.14
DI: P1.3, TP3.1, U2.11
DO: CON1.7 (DAT0), P1.5, TP6.1
GND: C1.2, C2.2, C3.2, C4.2, C5.2, CON1.3 (VSS), CON1.6 (VSS), CON1.12 (SHELL1), CON1.13 (SHELL2), D1.1 (K), P1.6, TP8.1, U1.2 (GND), U2.3, U2.5, U2.7, U2.8 (VSS)
unnamed: C1.1, L1.2, R1.1, U1.1 (VIN)
unnamed: C2.1, U1.4 (BYP)
unnamed: CON1.1 (CD/DAT3), U2.15
unnamed: CON1.2 (CMD), U2.12
unnamed: CON1.5 (CLK), U2.10
unnamed: D1.2 (A), R2.2
unnamed: R1.2, U1.3 (INH)

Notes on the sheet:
INPUT CONNECTOR
SD CARD SOCKET AND LEVEL SHIFTING
3.3v LDO

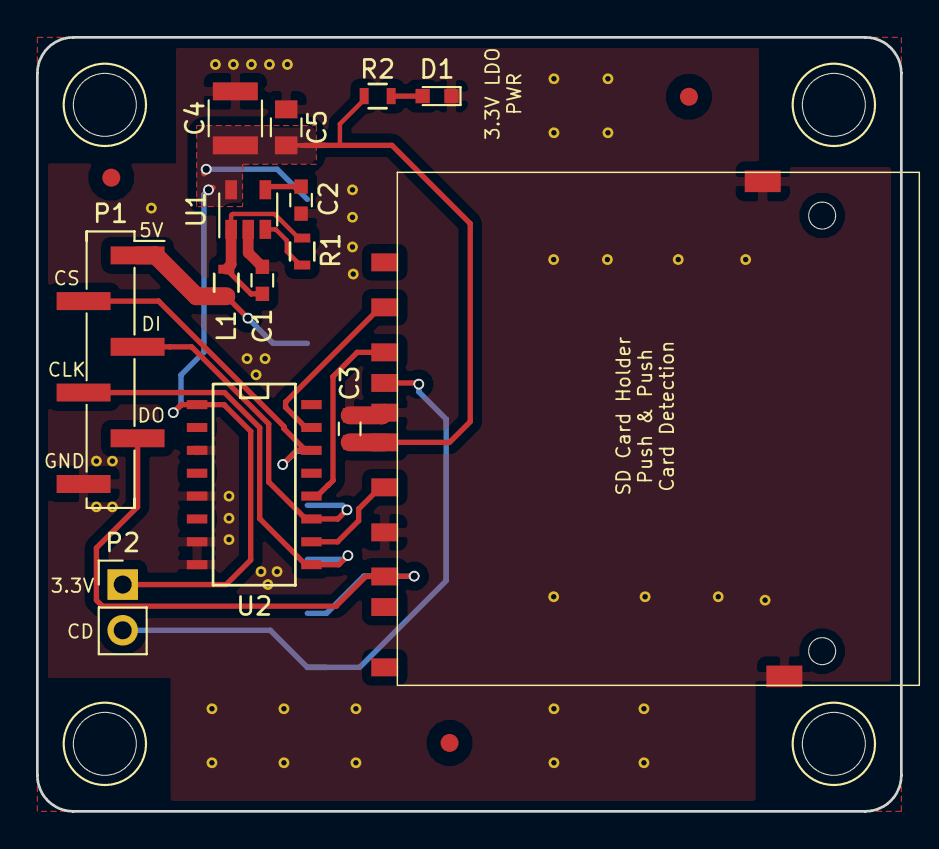
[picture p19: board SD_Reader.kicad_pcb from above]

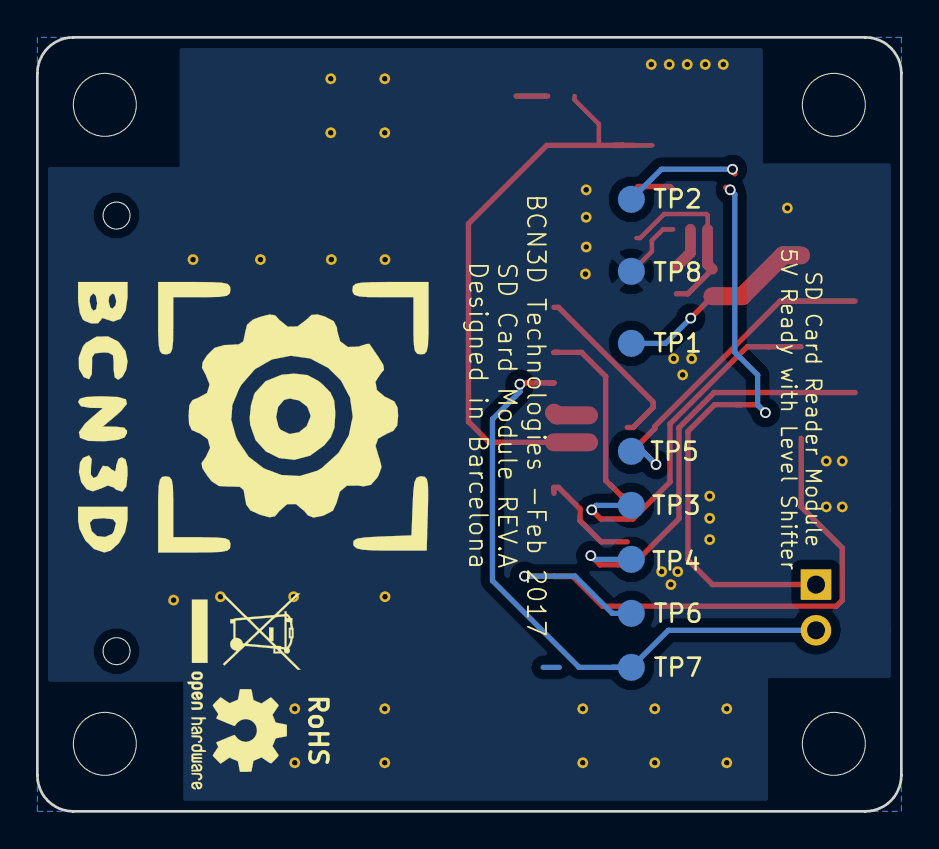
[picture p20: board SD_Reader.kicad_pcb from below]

Board: 2 copper layers, 48.0 x 43.0 mm, 22 parts (8 on the bottom side), 15 nets.

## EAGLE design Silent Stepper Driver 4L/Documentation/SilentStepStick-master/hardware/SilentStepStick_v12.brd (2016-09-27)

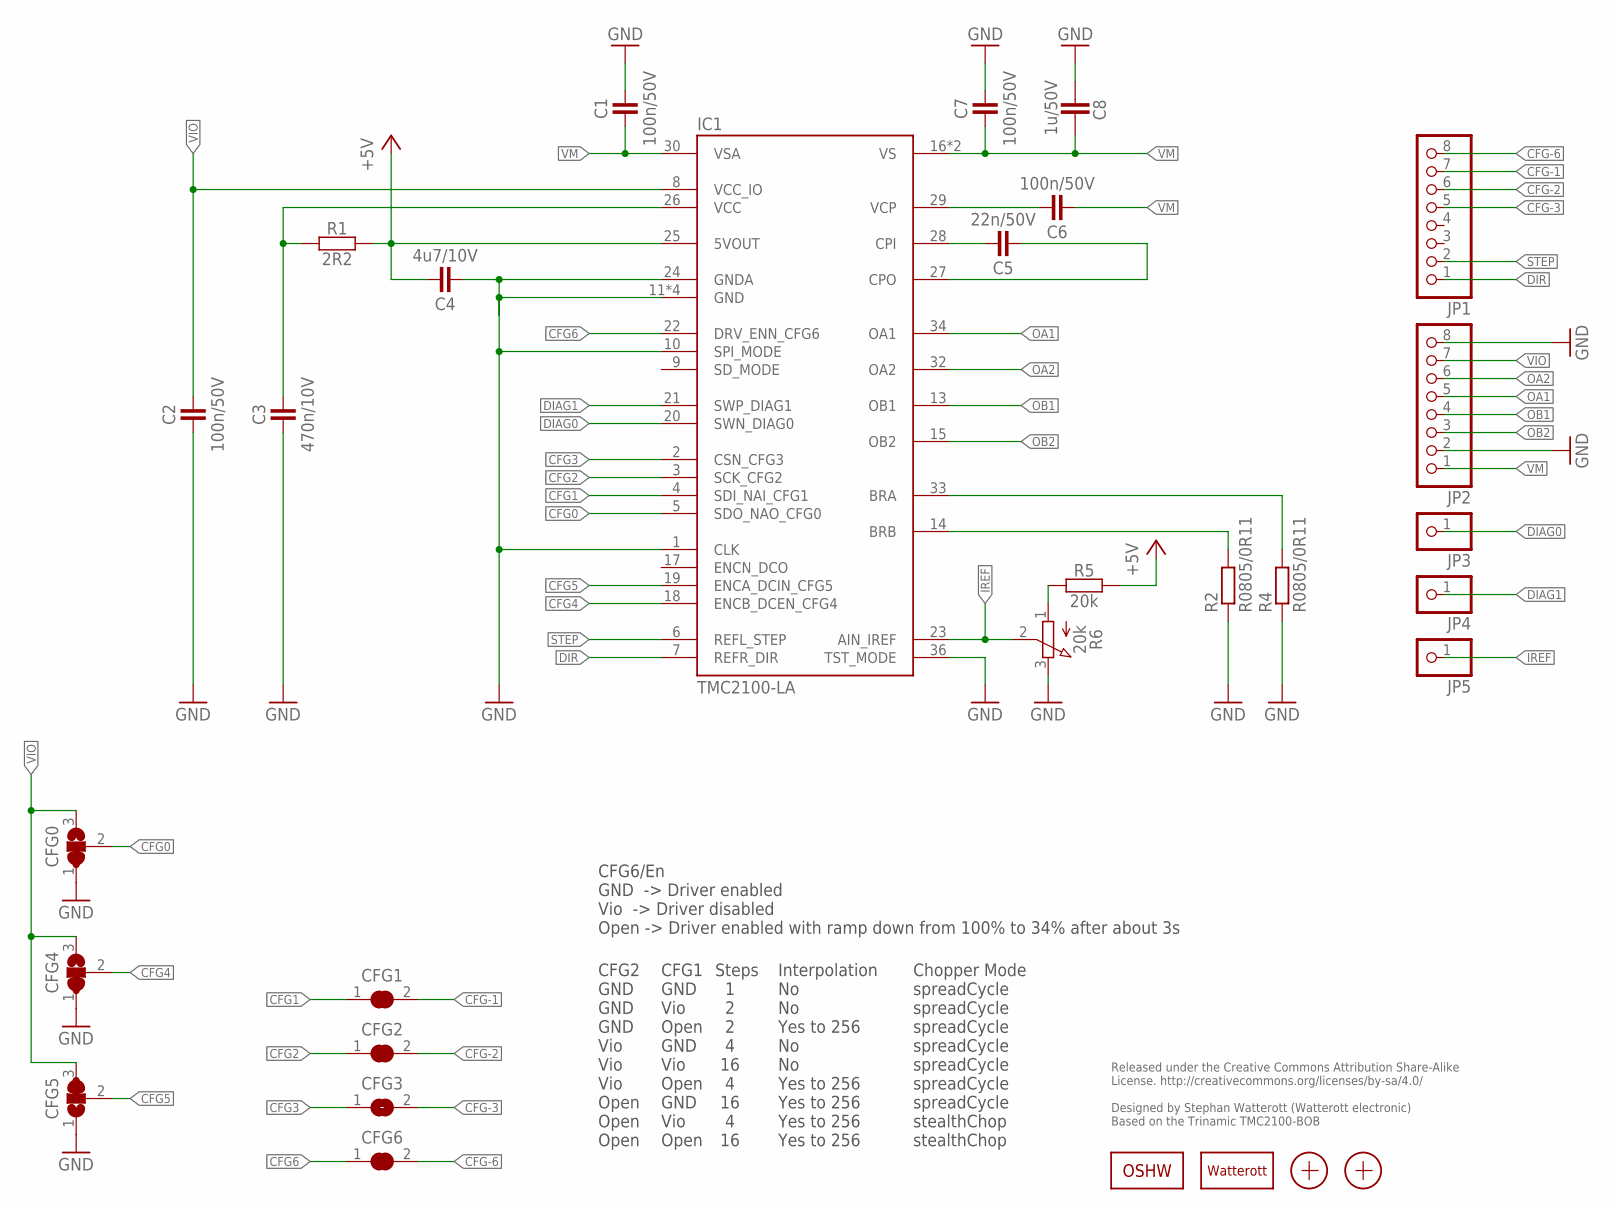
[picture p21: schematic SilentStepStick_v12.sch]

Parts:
C1, C2, C6, C7: 100n/50V; C0402
C3: 470n/10V; C0402
C4: 4u7/10V; C0402
C5: 22n/50V; C0402
C8: 1u/50V; C0603
CFG0, CFG4, CFG5: JUMPER3-0201
CFG1, CFG2, CFG3, CFG6: JUMPER2-0201
IC1: TMC2100-LA; QFN36-PAD
JP1, JP2: PINHD-1X08_2.54-S; 1X08-S
JP3, JP4, JP5: PINHD-1X1; 1X01
LOGO1: OSHW_LOGOX0070; OSHW_6X70
LOGO2: LOGO-S_PLACE_M; SPARK_TPLACE_M
R1: 2R2; C0402
R2, R4: R0805/0R11; M0805
R5: 20k; C0402
R6: 20k; POT_EVM3R
X1, X2: PASSER-07; PASSER_07MM

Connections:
+5V: C4.2, IC1.25 (5VOUT), R1.2, R5.2
BRA: IC1.33 (BRA), R4.2
BRB: IC1.14 (BRB), R2.2
CFG0: CFG0.2, IC1.5 (SDO_NAO_CFG0)
CFG1: CFG1.1, IC1.4 (SDI_NAI_CFG1)
CFG2: CFG2.1, IC1.3 (SCK_CFG2)
CFG3: CFG3.1, IC1.2 (CSN_CFG3)
CFG4: CFG4.2, IC1.18 (ENCB_DCEN_CFG4)
CFG5: CFG5.2, IC1.19 (ENCA_DCIN_CFG5)
CFG6: CFG6.1, IC1.22 (DRV_ENN_CFG6)
CFG-1: CFG1.2, JP1.7
CFG-2: CFG2.2, JP1.6
CFG-3: CFG3.2, JP1.5
CFG-6: CFG6.2, JP1.8
CPI: C5.2, IC1.28 (CPI)
CPO: C5.1, IC1.27 (CPO)
DIAG0: IC1.20 (SWN_DIAG0), JP3.1
DIAG1: IC1.21 (SWP_DIAG1), JP4.1
DIR: IC1.7 (REFR_DIR), JP1.1
GND: C1.2, C2.1, C3.1, C4.1, C7.2, C8.2, CFG0.1, CFG4.1, CFG5.1, IC1.1 (CLK), IC1.10 (SPI_MODE), IC1.11 (GND), IC1.12 (GND), IC1.24 (GNDA), IC1.35 (GND), IC1.36 (TST_MODE), IC1.TP (GND), JP2.2, JP2.8, R2.1, R4.1, R6.3 (E)
IREF: IC1.23 (AIN_IREF), JP5.1, R6.2 (S)
OA1: IC1.34 (OA1), JP2.5
OA2: IC1.32 (OA2), JP2.6
OB1: IC1.13 (OB1), JP2.4
OB2: IC1.15 (OB2), JP2.3
STEP: IC1.6 (REFL_STEP), JP1.2
VCC: C3.2, IC1.26 (VCC), R1.1
VCP: C6.2, IC1.29 (VCP)
VIO: C2.2, CFG0.3, CFG4.3, CFG5.3, IC1.8 (VCC_IO), JP2.7
VM: C1.1, C6.1, C7.1, C8.1, IC1.16 (VS), IC1.30 (VSA), IC1.31 (VS), JP2.1
VREF1: R5.1, R6.1 (A)

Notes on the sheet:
Released under the Creative Commons Attribution Share-Alike License. http://creativecommons.org/licenses/by-sa/4.0/ Designed by Stephan Watterott (Watterott electronic) Based on the Trinamic TMC2100-BOB
CFG6/En GND -> Driver enabled Vio -> Driver disabled Open -> Driver enabled with ramp down from 100% to 34% after about 3s
CFG2 GND GND GND Vio Vio Vio Open Open Open
CFG1 GND Vio Open GND Vio Open GND Vio Open
Steps 1 2 2 4 16 4 16 4 16
Interpolation No No Yes to 256 No No Yes to 256 Yes to 256 Yes to 256 Yes to 256
Chopper Mode spreadCycle spreadCycle spreadCycle spreadCycle spreadCycle spreadCycle spreadCycle stealthChop stealthChop

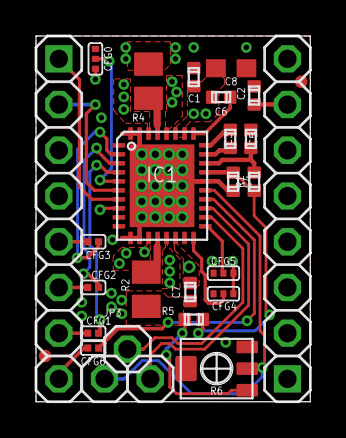
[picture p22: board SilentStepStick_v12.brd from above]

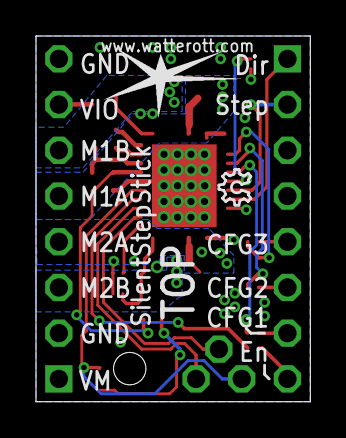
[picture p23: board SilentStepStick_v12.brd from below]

Board: 4 copper layers, 15.2 x 20.3 mm, 30 parts (2 on the bottom side), 31 nets.

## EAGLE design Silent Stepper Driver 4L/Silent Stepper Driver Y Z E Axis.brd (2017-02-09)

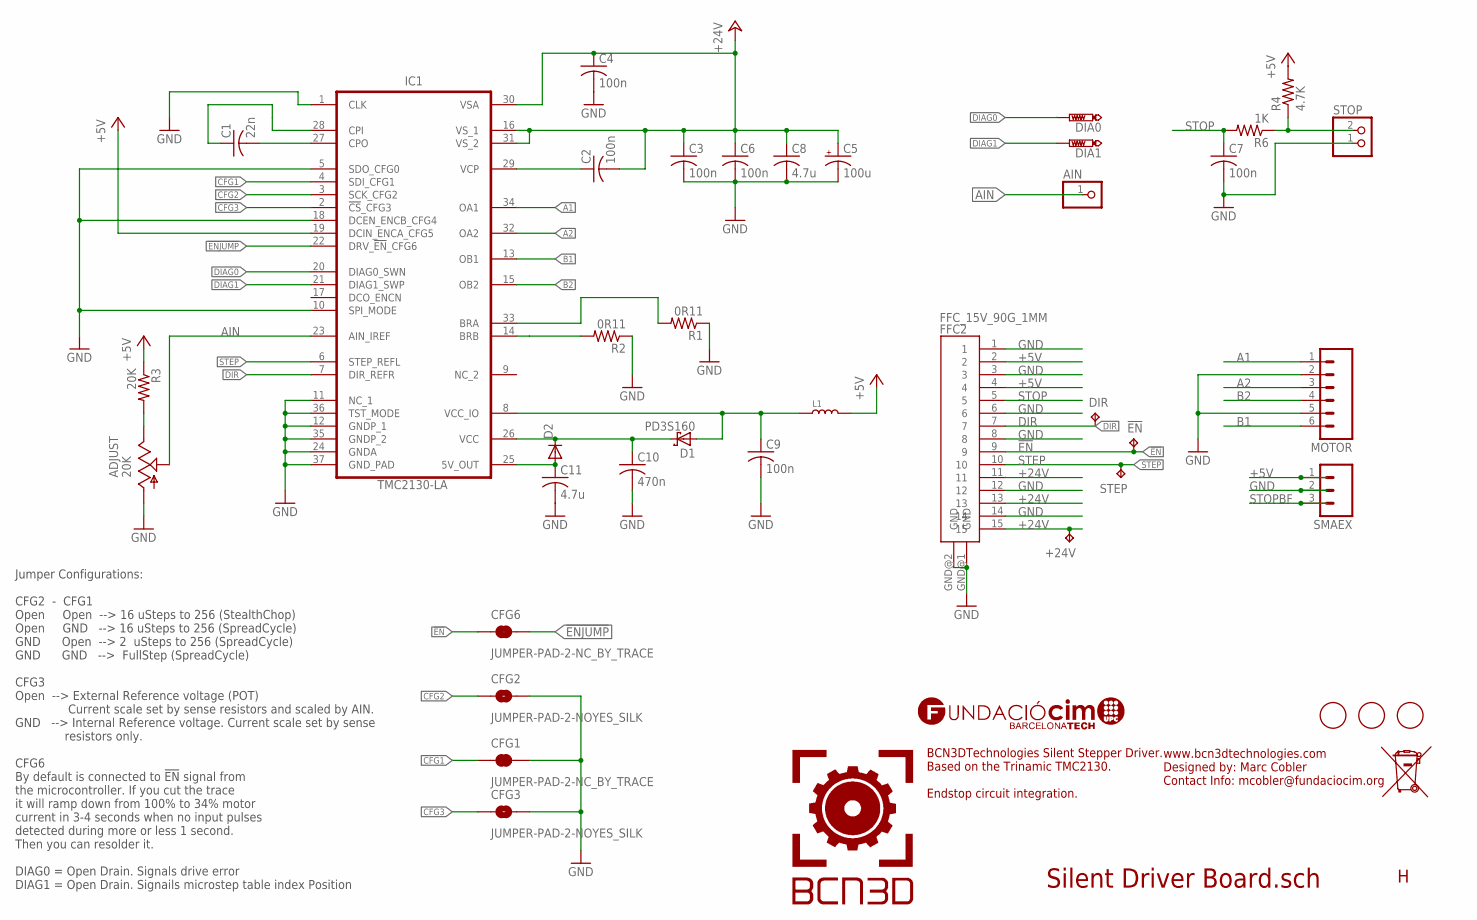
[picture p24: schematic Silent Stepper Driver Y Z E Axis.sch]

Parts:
!EN: TPB1,27; B1,27
+24V: TPB1,27; B1,27
ADJUST: 20K; 3223G; MPN 3314G-2-203E
AIN: PINHD-1X1; 1X01
C1: 22n; C0603K; MPN GCM188R72A223KA37D
C2, C3, C4, C6, C7, C9: 100n; C0603K; MPN 06035C104KAT2A
C5: 100u; UD-6,3X7,7_NICHICON; MPN EEE1HA101UAP
C8: 4.7u; C1210; MPN C1210X475K5RACTU
C10: 470n; C0603K; MPN GRM188R71C474KA88D
C11: 4.7u; C0805; MPN 0805YC475KAT2A
CFG1, CFG6: JUMPER-PAD-2-NC_BY_TRACE; PAD-JUMPER-2-NC_BY_TRACE_YES_SILK
CFG2, CFG3: JUMPER-PAD-2-NOYES_SILK; PAD-JUMPER-2-NO_YES_SILK
D1: PD3S160; POWERDI323; MPN PD3S160-7
D2: DIODE-MINIMELF; MINIMELF; MPN PMLL4448
DIA0, DIA1: PTR1TP12R; TP12R
DIR: TPB1,27; B1,27
FFC2: FFC_15V_90G_1MM; TE_FFC_CON1MM
IC1: TMC2130-LA; TMC_QFN36_0.5_5.0X6.0
L1: INDUCTOR/FERRITE-BEAD'0603'; L0603; MPN CRL0603-FW-R470ELF
MOTOR: M06; JST-6-PTH; MPN S6B-PH-K-S (LF)(SN)
R1, R2: 0R11; R0805; MPN ERJ6BSFR11V
R3: 20K; R0603; MPN MC0201L6F2002SE.
R4: 4.7K; R0603; MPN ERJP06F4701V
R6: 1K; R0603; MPN CR0805-JW-102ELF
SMAEX: M03PTH; 1X03
STEP: TPB1,27; B1,27
STOP: JST_2PIN-THM-RA; JST-PH-2-THM-RA; MPN S2B-PH-K-S (LF)(SN)
U$2, U$3, U$4: FIDUCIAL; FIDUCIAL_1MM

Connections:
!EN: !EN.TP, CFG6.1, FFC2.9
!ENJUMP: CFG6.2, IC1.22 (DRV_!EN!_CFG6)
+5V: FFC2.2, FFC2.4, IC1.19 (DCIN_ENCA_CFG5), L1.2, R3.1, R4.2, SMAEX.1
+24V: +24V.TP, C2.2, C3.1, C4.1, C5.+, C6.1, C8.1, FFC2.11, FFC2.13, FFC2.15, IC1.16 (VS_1), IC1.30 (VSA), IC1.31 (VS_2)
A1: IC1.34 (OA1), MOTOR.1
A2: IC1.32 (OA2), MOTOR.3
AIN: ADJUST.2 (S), AIN.1, IC1.23 (AIN_IREF)
B1: IC1.13 (OB1), MOTOR.6
B2: IC1.15 (OB2), MOTOR.4
CFG1: CFG1.1, IC1.4 (SDI_CFG1)
CFG2: CFG2.1, IC1.3 (SCK_CFG2)
CFG3: CFG3.1, IC1.2 (!CS!_CFG3)
DIAG0: DIA0.TP, IC1.20 (DIAG0_SWN)
DIAG1: DIA1.TP, IC1.21 (DIAG1_SWP)
DIR: DIR.TP, FFC2.7, IC1.7 (DIR_REFR)
GND: ADJUST.1 (A), C3.2, C4.2, C5.-, C6.2, C7.2, C8.2, C9.2, C10.2, C11.2, CFG1.2, CFG2.2, CFG3.2, FFC2.1, FFC2.3, FFC2.6, FFC2.8, FFC2.12, FFC2.14, FFC2.GND@1 (GND), FFC2.GND@2 (GND), IC1.1 (CLK), IC1.5 (SDO_CFG0), IC1.10 (SPI_MODE), IC1.11 (NC_1), IC1.12 (GNDP_1), IC1.18 (DCEN_ENCB_CFG4), IC1.24 (GNDA), IC1.35 (GNDP_2), IC1.36 (TST_MODE), IC1.37 (GND_PAD), MOTOR.2, MOTOR.5, R1.1, R2.1, SMAEX.2, STOP.1 (2)
unnamed: C1.2, IC1.27 (CPO)
unnamed: C1.1, IC1.28 (CPI)
unnamed: C2.1, IC1.29 (VCP)
unnamed: C11.1, D2.A, IC1.25 (5V_OUT)
unnamed: ADJUST.3 (E), R3.2
unnamed: C10.1, D1.C, D2.C, IC1.26 (VCC)
unnamed: IC1.33 (BRA), R1.2
unnamed: IC1.14 (BRB), R2.2
unnamed: C9.1, D1.A, IC1.8 (VCC_IO), L1.1
STEP: FFC2.10, IC1.6 (STEP_REFL), STEP.TP
STOP: C7.1, FFC2.5, R6.2
STOPBF: R4.1, R6.1, SMAEX.3, STOP.2 (1)

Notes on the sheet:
Silent Driver Board.sch
BCN3DTechnologies Silent Stepper Driver. Based on the Trinamic TMC2130. Endstop circuit integration.
www.bcn3dtechnologies.com Designed by: Marc Cobler Contact Info: mcobler@fundaciocim.org
Jumper Configurations: CFG2 - CFG1 Open Open --> 16 uSteps to 256 (StealthChop) Open GND --> 16 uSteps to 256 (SpreadCycle) GND Open --> 2 uSteps to 256 (SpreadCycle) GND GND --> FullStep (SpreadCycle) CFG3 Open --> External Reference voltage (POT) Current scale set by sense resistors and scaled by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

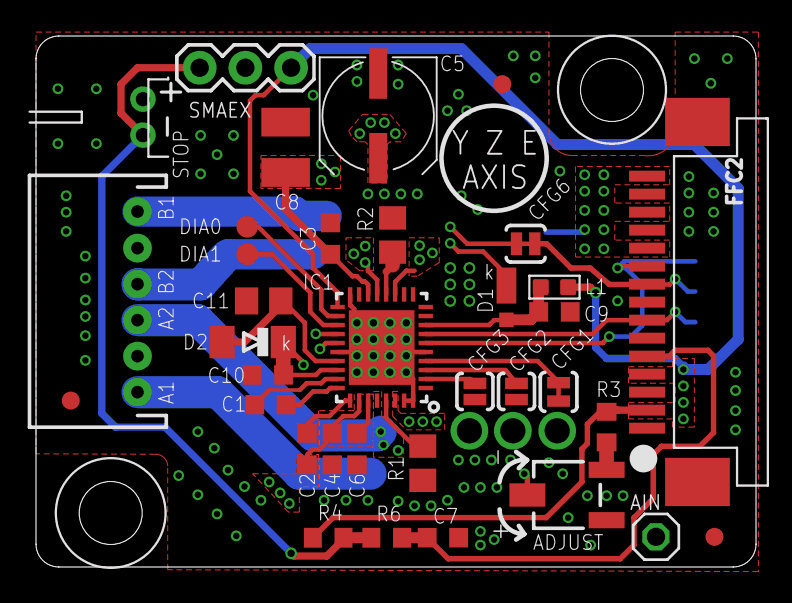
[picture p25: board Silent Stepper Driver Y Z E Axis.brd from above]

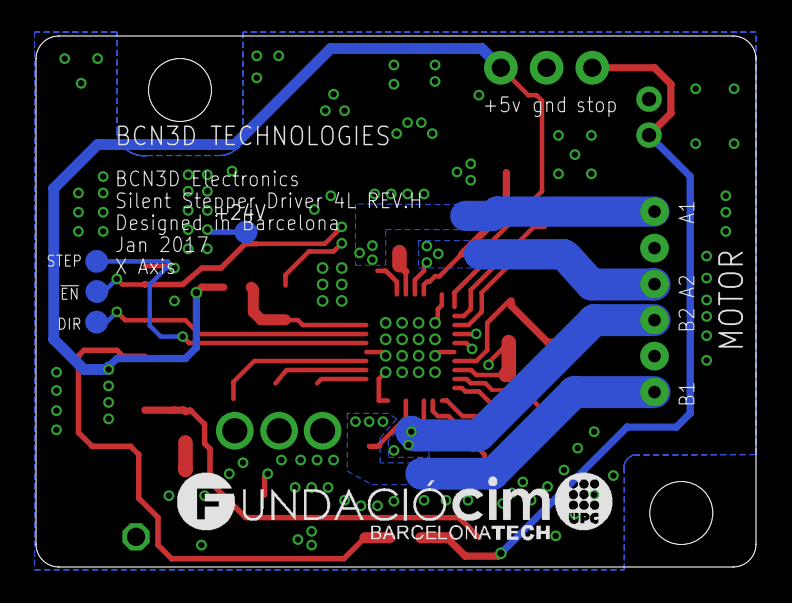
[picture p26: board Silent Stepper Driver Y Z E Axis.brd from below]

Board: 4 copper layers, 40.0 x 29.5 mm, 40 parts (5 on the bottom side), 28 nets.

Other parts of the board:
U$5: FCIM_LOGO

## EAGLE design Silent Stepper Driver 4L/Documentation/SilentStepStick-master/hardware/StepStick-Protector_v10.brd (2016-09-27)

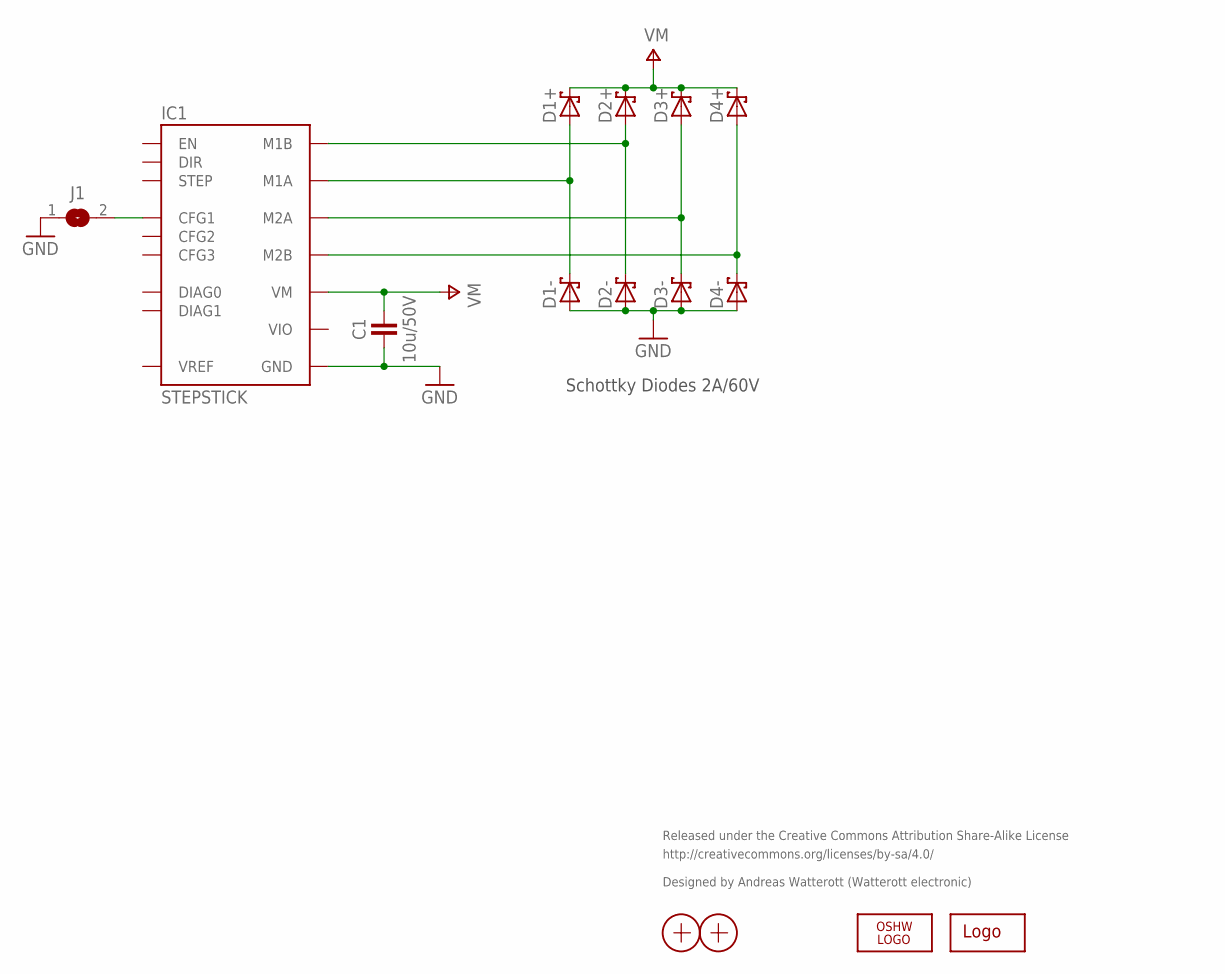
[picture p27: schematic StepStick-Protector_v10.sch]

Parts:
C1: 10u/50V; C1210
D1+, D1-, D2+, D2-, D3+, D3-, D4+, D4-: D_SCHOTTKY-SS14; SMA_DO214AC
IC1: STEPSTICK
J1: JUMPER2-0603-NC; JUMPER2-0603_NC
LOGO1: OSHW_LOGOX0070; OSHW_6X70
LOGO2: LOGO-S_PLACE_S; SPARK_TPLACE_S
X1, X2: PASSER

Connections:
GND: C1.1, D1-.A, D2-.A, D3-.A, D4-.A, IC1.GND@1 (GND), IC1.GND@2 (GND), J1.1
M1A: D1+.A, D1-.C, IC1.M1A
M1B: D2+.A, D2-.C, IC1.M1B
M2A: D3+.A, D3-.C, IC1.M2A
M2B: D4+.A, D4-.C, IC1.M2B
unnamed: IC1.CFG1, J1.2
VIO: IC1.VIO
VM: C1.2, D1+.C, D2+.C, D3+.C, D4+.C, IC1.VM

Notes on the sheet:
Released under the Creative Commons Attribution Share-Alike License
http://creativecommons.org/licenses/by-sa/4.0/
Designed by Andreas Watterott (Watterott electronic)
Schottky Diodes 2A/60V

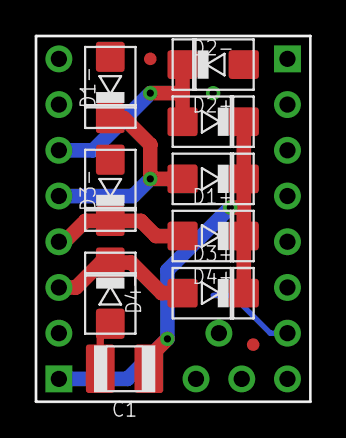
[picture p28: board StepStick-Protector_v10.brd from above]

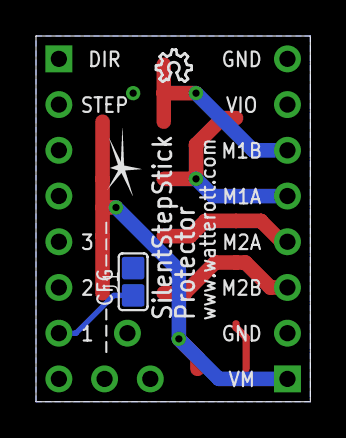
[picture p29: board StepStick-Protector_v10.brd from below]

Board: 2 copper layers, 15.2 x 20.3 mm, 15 parts (3 on the bottom side), 7 nets.

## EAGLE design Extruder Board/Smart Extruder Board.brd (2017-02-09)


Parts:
5V, 24V: TPB1,27; B1,27
C1, C2: 100n; C0603K; MPN 06035C104KAT2A
C3: 330n; C0805; MPN GRM219R71H334KA88D
CFAN: JST_2MM_MALE; JST-2-SMD; MPN S2B-PH-SM4-TB(LF)(SN)
CFAN+: TPB1,27; B1,27
CFAN-: TPB1,27; B1,27
CN1: JST_4PINPA; JST_PA_04; MPN SM04B-PASS-TBT(LF)(SN)
D1: PD3S160; POWERDI323; MPN PD3S160-7
ENDSTOP: JST_2MM_MALE; JST-2-SMD; MPN S2B-PH-SM4-TB(LF)(SN)
GND: TPB1,27; B1,27
L1: 1k; R0603; MPN MCMR06X1001FTL
LFAN: JST_2MM_MALE; JST-2-SMD; MPN S2B-PH-SM4-TB(LF)(SN)
Q1: BC807W; SOT323-BEC; MPN BC807W,115
Q2: MOSFET-NSOT323; SOT323; MPN PMF370XN,115
R1: 100; R1210; MPN MC0603SAF330JT5E
R2, R8: 10k; R0603; MPN MCMR06X1002FTL
R3: 5k23; R0603; MPN ERJ3EKF5231V
R4, R6: 1k; R0603; MPN MCMR06X1001FTL
R5: 200k; R0603; MPN ERJ3EKF2003V
R7: 22.6K; R0603; MPN MC0603SAF330JT5E
THERM: TPB1,27; B1,27
U2: LM3480IM4; SOT23-3; MPN LM3480IM3-12/NOPB
U3: LM392MMSOP8; MSOP8
U$1, U$2, U$3: FIDUCIAL; FIDUCIAL_1MM
VERT_FFC1: 68612014422

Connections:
12V: C2.2, CFAN.2 (+), CFAN+.TP, D1.C, Q1.3 (C), R6.2, U2.1 (OUT)
+5V: 5V.TP, L1.1, VERT_FFC1.1
+24V: 24V.TP, CN1.1, LFAN.2 (+), Q1.2 (E), R1.1, VERT_FFC1.8, VERT_FFC1.10, VERT_FFC1.12, VERT_FFC1.18, VERT_FFC1.19
DRAIN: CFAN.1 (-), CFAN-.TP, D1.A, Q2.3 (D)
GND: C1.2, C2.1, C3.1, ENDSTOP.1 (-), GND.TP, Q2.2 (S), R2.1, R8.1, U2.3 (GND), U3.4 (GND), VERT_FFC1.4, VERT_FFC1.7, VERT_FFC1.9, VERT_FFC1.11, VERT_FFC1.17
GNDTHERM: CN1.4, VERT_FFC1.2
HOTEND: CN1.2, VERT_FFC1.13, VERT_FFC1.14, VERT_FFC1.15, VERT_FFC1.16
HOTEND_THERM: CN1.3, THERM.TP, U3.5 (POS_B), VERT_FFC1.3
IN: C3.2, R1.2, R7.1, U2.2 (IN)
LFAN: LFAN.1 (-), VERT_FFC1.5, VERT_FFC1.6
unnamed: Q1.1 (B), R7.2
unnamed: C1.1, L1.2, R3.2, U3.8 (V+)
unnamed: U3.2 (NEG_A), U3.6 (NEG_B), U3.7 (OUT_B)
unnamed: R2.2, R3.1, R4.2
unnamed: R4.1, R5.2, U3.3 (POS_A)
OUT: Q2.1 (G), R5.1, R6.1, R8.2, U3.1 (OUT_A)
Z-ENDSTOP: ENDSTOP.2 (+), VERT_FFC1.20

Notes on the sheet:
INPUT
OUTPUT
BCN3D Technologies Extruder Board Autonomous cooler fan control
www.bcn3dtechnologies.com Designed by: Marc Cobler Contact Info: mcobler@fundaciocim.org
TEMPERATURE COMPARATOR
12V POWER SUPPLY



Board: 2 copper layers, 32.9 x 32.8 mm, 33 parts (8 on the bottom side), 17 nets.

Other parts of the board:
U$5: OSHW-LOGO-S
U$6: FCIM_LOGO

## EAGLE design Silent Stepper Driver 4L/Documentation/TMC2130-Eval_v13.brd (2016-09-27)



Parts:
INTERFACE_TO_UC/MC: FEMALE_HEADER_SMD_2.54_44_PINSHORTPADS_HOLES; FEMALE_HEADER_SMD_254_44_PIN_SHORTPADS_HOLES
MOTOR1: AKL182_04_POL_HEADER; AKL169_04_POL
PROBE_GND, PROBE_GND1, PROBE_GND2, PROBE_GND3: NOT ASSEMBLED; 1PIN_1ROW_THT
PWR: AKL_349_02_POL_HEADER; AKL349_02_POL
TERM1: AKL_330_2_POL_TERMINAL; EXTRA_TERMINAL
TERM2: AKL182_04_POL_TERMINAL; EXTRA_TERMINAL
TEST_POINT1, TEST_POINT2, TEST_POINT3, TEST_POINT4, TEST_POINT5, TEST_POINT6, TEST_POINT7, TEST_POINT8, TEST_POINT9, TEST_POINT10, TEST_POINT11, TEST_POINT12, TEST_POINT13, TEST_POINT14: NOT ASSEMBLED; PAD_R1.2

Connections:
+3V3: TEST_POINT1.P$1; also elsewhere on the board
+5V_USB: INTERFACE_TO_UC/MC.5; also elsewhere on the board
AIN_REF_PWM: INTERFACE_TO_UC/MC.22; also elsewhere on the board
AIN_REF_SW: INTERFACE_TO_UC/MC.21; also elsewhere on the board
CLK: INTERFACE_TO_UC/MC.23; also elsewhere on the board
CSN_CFG3: INTERFACE_TO_UC/MC.24; also elsewhere on the board
DRV_ENN_CFG6: INTERFACE_TO_UC/MC.8; also elsewhere on the board
ENCA_DCIN_CFG5: INTERFACE_TO_UC/MC.34; also elsewhere on the board
ENCB_DCEN_CFG4: INTERFACE_TO_UC/MC.35; also elsewhere on the board
ENCN_DCO: INTERFACE_TO_UC/MC.36; also elsewhere on the board
GND: INTERFACE_TO_UC/MC.2, INTERFACE_TO_UC/MC.3, INTERFACE_TO_UC/MC.43, INTERFACE_TO_UC/MC.44, PROBE_GND.1, PROBE_GND1.1, PROBE_GND2.1, PROBE_GND3.1, PWR.1, TEST_POINT14.P$1; also elsewhere on the board
ID_CH1: INTERFACE_TO_UC/MC.7; also elsewhere on the board
ID_CLK: INTERFACE_TO_UC/MC.4; also elsewhere on the board
INT_DIR: INTERFACE_TO_UC/MC.18; also elsewhere on the board
INT_STEP: INTERFACE_TO_UC/MC.17; also elsewhere on the board
M1A: MOTOR1.3; also elsewhere on the board
M1A2: MOTOR1.4; also elsewhere on the board
M1B1: MOTOR1.1; also elsewhere on the board
M1B2: MOTOR1.2; also elsewhere on the board
SCK_CFG2: INTERFACE_TO_UC/MC.27; also elsewhere on the board
SDI_NAI_CFG1: INTERFACE_TO_UC/MC.29; also elsewhere on the board
SDO_NAO_CFG0: INTERFACE_TO_UC/MC.28; also elsewhere on the board
SENSEA: TEST_POINT2.P$1; also elsewhere on the board
SENSEB: TEST_POINT3.P$1; also elsewhere on the board
SEP_DIAG1: INTERFACE_TO_UC/MC.38; also elsewhere on the board
SWN_DIAG0: INTERFACE_TO_UC/MC.37; also elsewhere on the board
VM: INTERFACE_TO_UC/MC.1, PWR.2; also elsewhere on the board

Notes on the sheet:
Motion
Controller
Driver Board
Testpoints for functional testing.
Please apply all generated supply voltages and relevant signals.
Please keep positions of all interconnectors if not absolutely imposseble.
Changes to v13 (2015-07-20)
- Adapted footprint to avoid of production issues(noncritical)
- minor changes of design resulting from adaption of footprint

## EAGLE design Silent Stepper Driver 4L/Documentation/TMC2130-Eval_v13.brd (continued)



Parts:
AIN_REF: NOT ASSEMBLED; 1PIN_1ROW_THT
C1, C2: 0603/4.7µF/10V; RCL_0603
C3: 0603/10nF/10V; RCL_0603
C5, C7, C10, C15: C0603/100nF/50V; C0603
C6: C0603/4µ7/16V; C0603
C8: C0603/22nF/50V; C0603
C9: C0603/470nF/16V; C0603
C11: 1210/4.7uF/100V; C1210
C12, C13: EEUFR1J151 150uF/63V/0R045; C_POL_RAD_THT_5X10X12.5
C14: 0805/4µ7/50V; C0805
C_ID: C_ID/10V/1%; RCL_0603
D1: SMBJ43A; SMB
D3, D4: BAT54S; SOT23
IC1: SN74LVC1G123DCTR
IC2: LP2985AIM5-3.3; SOT23-5
JMP1: JUMPER_2.54MM BLACK ON X2; EXTRA_TERMINAL
JMP2: JUMPER_2.54MM BLACK ON X1; EXTRA_TERMINAL
R1: 0603/10k/1%; RCL_0603
R2: 10K; RCL_0603
R5, R7: R1206,0R22/0.5W; R1206
R6: 0603/2R2/1%; R0603
R8: NOT ASSEMBLED; R0603
R9: 0603/0R; R0603
R10: 10k/0603/1%; RCL_0603
R11: 15k/0603/1%; RCL_0603
R12, R13: 0603/10k/1%; 0603
R14, R15: 0603/1k/1%; 0603
R17: 4k7/0603/1%; RCL_0603
REF2: MALE HEADER 2.54; 3PIN_1ROW_2,54_THT
RSENSE_A: NOT ASSEMBLED; 1PIN_1ROW_THT
RSENSE_B: NOT ASSEMBLED; 1PIN_1ROW_THT
R_ID: R_ID/1%; RCL_0603
R_SD: NOT_ASSEMBLED; RCL_0603
R_SPI: NOT_ASSEMBLED; RCL_0603
TMC2130: TMC2130_QFN36; QFN36
X1, X2: MALE HEADER 2.54; 3PIN_1ROW_2,54_THT

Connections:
+3V3: C2.1, IC1.8 (VCC), IC2.5 (OUT), R2.1, R9.1, R_ID.2; also elsewhere on the board
+5V_USB: C1.1, IC2.1 (IN), IC2.3 (ON), R8.2; also elsewhere on the board
AIN_REF: AIN_REF.1, R10.2, R11.2, TMC2130.23 (AIN_IREF)
AIN_REF_PWM: R17.1; also elsewhere on the board
AIN_REF_SW: R11.1; also elsewhere on the board
CLK: TMC2130.1 (CLK); also elsewhere on the board
CSN_CFG3: TMC2130.2 (CSN_CFG3); also elsewhere on the board
DRV_ENN_CFG6: TMC2130.22 (DRV_ENN_CFG6); also elsewhere on the board
ENCA_DCIN_CFG5: TMC2130.19 (ENCA_DCIN_CFG5); also elsewhere on the board
ENCB_DCEN_CFG4: TMC2130.18 (ENCB_DCEN_CFG4); also elsewhere on the board
ENCN_DCO: TMC2130.17 (ENCN_DCO); also elsewhere on the board
EXT_DIR: D3.3 (C1A2), R14.2, X2.1
EXT_DIR_CON: R12.2, R14.1, REF2.1
EXT_STEP: D4.3 (C1A2), R15.2, X1.1
EXT_STEP_CON: R13.2, R15.1, REF2.2
GND: C1.2, C2.2, C3.2, C5.2, C6.2, C9.1, C10.1, C11.2, C12.-, C13.-, C14.1, C15.1, C_ID.2, D1.A, D3.1 (A1), D4.1 (A1), IC1.1 (!A), IC1.4 (GND), IC1.6 (C_EXT), IC2.2 (GND), R1.2, R5.1, R7.1, R12.1, R13.1, REF2.3, R_SD.1, R_SPI.1, TMC2130.11 (GND), TMC2130.12 (GND), TMC2130.24 (GNDA), TMC2130.35 (GND), TMC2130.36 (TST_MODE), TMC2130.GND_PAD (GND); also elsewhere on the board
ID_CH1: IC1.5 (Q); also elsewhere on the board
ID_CLK: IC1.2 (B), R1.1; also elsewhere on the board
INT_DIR: X2.3; also elsewhere on the board
INT_STEP: X1.3; also elsewhere on the board
M1A: TMC2130.34 (OA1); also elsewhere on the board
M1A2: TMC2130.32 (OA2); also elsewhere on the board
M1B1: TMC2130.13 (OB1); also elsewhere on the board
M1B2: TMC2130.15 (OB2); also elsewhere on the board
unnamed: C3.1, IC1.3 (!CLR), R2.2
unnamed: C_ID.1, IC1.7 (C_EXT/R_EXT), R_ID.1
unnamed: R_SPI.2, TMC2130.10 (SPI_MODE)
unnamed: R_SD.2, TMC2130.9 (DNC)
unnamed: C6.1, R6.1, TMC2130.25 (5VOUT)
unnamed: C8.1, TMC2130.28 (CPI)
unnamed: C8.2, TMC2130.27 (CPO)
unnamed: C7.2, TMC2130.29 (VCP)
unnamed: C9.2, R6.2, TMC2130.26 (VCC)
unnamed: C14.2, R10.1, R17.2
SCK_CFG2: TMC2130.3 (SCK_CFG2); also elsewhere on the board
SDI_NAI_CFG1: TMC2130.4 (SDI_NAI_CFG1); also elsewhere on the board
SDO_NAO_CFG0: TMC2130.5 (SDO_NAO_CFG0); also elsewhere on the board
SENSEA: R5.2, RSENSE_A.1, TMC2130.33 (BRA); also elsewhere on the board
SENSEB: R7.2, RSENSE_B.1, TMC2130.14 (BRB); also elsewhere on the board
SEP_DIAG1: TMC2130.21 (SWP_DIAG1); also elsewhere on the board
SWN_DIAG0: TMC2130.20 (SWN_DIAG0); also elsewhere on the board
VCC_IO: C5.1, D3.2 (C2), D4.2 (C2), R8.1, R9.2, TMC2130.8 (VCC_IO)
VM: C7.1, C10.2, C11.1, C12.+, C13.+, C15.2, D1.C, TMC2130.16 (VS), TMC2130.30 (VSA), TMC2130.31 (VS); also elsewhere on the board
[REFL]_STEP: TMC2130.6 (REFL_STEP), X1.2
[REFR]_DIR: TMC2130.7 (REFR_DIR), X2.2



Board: 4 copper layers, 55.0 x 85.0 mm, 71 parts (15 on the bottom side), 45 nets.

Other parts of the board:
U$1: TMC_EVAL_RIGHT_BAR
U$3: TMC_EVAL_BACK_NO_DOCU

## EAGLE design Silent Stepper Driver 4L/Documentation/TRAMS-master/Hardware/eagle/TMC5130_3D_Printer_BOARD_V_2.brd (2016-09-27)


Board: 4 copper layers, 110.0 x 61.0 mm, 147 parts (1 on the bottom side), 137 nets.

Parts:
AUX-1, AUX-3: 2X4
AUX-2: AVR_ICSP
AUX-4: 1X18
C1, C40, C44, C45, C46, C47, C48, C49: 1nF; 0603
C2, C3, C5, C7, C10, C12, C13, C14, C15, C16, C18, C20, C22, C24, C26, C28, C30, C32, C34, C36, C38, C39, C41: 100nF; C0603
C4, C6, C11, C19, C23, C27, C31, C35: 4.7µF; C0603
C8, C17, C25, C33: 22nF; C0603
C9, C21, C37: 470nF; 0603
C29: C0603/470nF/16V; C0603
C42, C43: 1000µ 30V; E5-10,5
D2, D4, D5, D6: SMBJ43A; SMB
D_HB, D_HB1, D_HB2: MSS1P6; MICRO_SMP
E0_ENDSTOP: 5PIN_1ROWTHT; 5PIN_1ROW_2.54_THT
E0_MOTOR: 4PIN_1ROW_2.54_THT
EX_0: RIA_AKL_220_2_PINS
F1, F2: LITTLEFUSE_TR5_383_SERIES
FAN: RIA_AKL_220_2_PINS
HEATBED: RIA_AKL_220_2_PINS
I2C: 1X04
IC1, IC2, IC6: SN74LVC3G17DCUR; US8_DCU
LED1, LED4, LED6: RED; CHIPLED_0603
LED2, LED3: GREEN; CHIPLED_0603
MAIN_IN: RIA_AKL_220_4_PINS
R1, R2, R3, R19, R20, R21, R24, R26, R27, R28, R29, R33, R34: 4.7kΩ; R0603
R4, R8, R9, R22, R23, R25, R30, R31, R32: 100Ω; R0603
R5, R7, R10, R11, R13, R14, R16, R17: R1206,0R15/0.5W; R1206
R6, R12, R15, R18: 2.2Ω; 0603
RL2, RL3: 4.7kΩ; R0603
R_PD6, R_PD7, R_PD8, R_PD9, R_PD10, R_PD11, R_PD12, R_PD13: 100kΩ; R0603
S1: B3F-10XX
SERVO: 1X04
SERV_SUPPLY: 2X4
SHIELD: ARDUINO_MEGA_SHIELD_BIG; ARDUINO_MEGA_SHIELD
T1, T2, T3: AON7508; DFN3X3_8L
THERM0, THERM1, THERM2: 2PIN_1ROW; 2PIN_1ROW_2.54_THT
TMC1, TMC2, TMC3, TMC5130: QFP50P900X900X113-49N_NOFID
U$10: TRINAMIC_LOGO_WHITE_NOTEXT
U$11: TRAMS_PRINT
VM0, VM1: 2PIN_1ROW; 2PIN_1ROW_2.54_THT
XTAL: SM77H 16MHz; SM77H
X_ENDSTOP: 5PIN_1ROWTHT; 5PIN_1ROW_2.54_THT
X_MOTOR: 4PIN_1ROW_2.54_THT
Y_ENDSTOP: 5PIN_1ROWTHT; 5PIN_1ROW_2.54_THT
Y_MOTOR: 4PIN_1ROW_2.54_THT
Z_ENDSTOP: 5PIN_1ROWTHT; 5PIN_1ROW_2.54_THT
Z_MOTOR_1, Z_MOTOR_2: 4PIN_1ROW_2.54_THT

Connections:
+5V: AUX-1.1, AUX-1.2, AUX-2.1, AUX-3.1, AUX-4.1, C1.2, C2.2, C3.1, C5.1, C22.1, C30.1, C38.1, C39.1, C40.2, C41.1, C44.2, C45.2, C46.2, C47.2, C48.2, C49.2, E0_ENDSTOP.2, E0_ENDSTOP.4, I2C.1, IC1.8, IC2.8, IC6.8, R1.2, R2.2, R3.2, R19.2, R20.2, R33.1, R34.1, SERV_SUPPLY.1, SERV_SUPPLY.3, SERV_SUPPLY.5, SERV_SUPPLY.7, SHIELD.5V@0, SHIELD.5V@1, SHIELD.5V@2, TMC1.10, TMC2.10, TMC3.10, TMC5130.10, XTAL.1, XTAL.4, X_ENDSTOP.2, X_ENDSTOP.4, Y_ENDSTOP.2, Y_ENDSTOP.4, Z_ENDSTOP.2, Z_ENDSTOP.4
A3: AUX-1.5, SHIELD.A3
A4: AUX-1.7, SHIELD.A4
A5: AUX-2.3, SHIELD.A5
A9: AUX-2.4, SHIELD.A9
A10: AUX-2.5, SHIELD.A10
A11: AUX-2.10, SHIELD.A11
A12: AUX-2.9, SHIELD.A12
CLK: TMC1.2, TMC2.2, TMC3.2, TMC5130.2, XTAL.3
CS_E0: SHIELD.47, TMC3.3
CS_X: SHIELD.46, TMC5130.3
CS_Y: SHIELD.49, TMC1.3
CS_Z: SHIELD.48, TMC2.3
D0: AUX-1.8, SHIELD.0
D1: AUX-1.6, SHIELD.1
D4: SERVO.4, SHIELD.4
D5: SERVO.3, SHIELD.5
D6: SERVO.2, SHIELD.6
D11: SERVO.1, SHIELD.11
D16: AUX-4.18, SHIELD.16
D17: AUX-4.17, SHIELD.17
D23: AUX-4.16, SHIELD.23
D25: AUX-4.15, SHIELD.25
D27: AUX-4.14, SHIELD.27
D29: AUX-4.13, SHIELD.29
D31: AUX-4.12, SHIELD.31
D32: AUX-4.3, SHIELD.32
D33: AUX-4.11, SHIELD.33
D34: AUX-3.2, SHIELD.34
D35: AUX-4.10, SHIELD.35
D36: AUX-4.4, SHIELD.36
D37: AUX-4.9, SHIELD.37
D39: AUX-4.8, SHIELD.39
D40: AUX-2.6, SHIELD.40
D41: AUX-4.7, SHIELD.41
D42: AUX-2.8, SHIELD.42
D43: AUX-4.6, SHIELD.43
D44: AUX-2.7, SHIELD.44
D45: AUX-4.5, SHIELD.45
D53: AUX-3.6, SHIELD.53
DRV_EN_E0: SHIELD.24, TMC3.29
DRV_EN_X: SHIELD.38, TMC5130.29
DRV_EN_Y: SHIELD.A8, TMC1.29
DRV_EN_Z: SHIELD.A2, TMC2.29
ENDSTOP_E0_LEFT: C49.1, E0_ENDSTOP.5, R_PD12.2, TMC3.8
ENDSTOP_E0_RIGHT: C48.1, E0_ENDSTOP.1, R_PD13.2, TMC3.9
ENDSTOP_X_LEFT: C45.1, R_PD6.2, TMC5130.8, X_ENDSTOP.5
ENDSTOP_X_RIGHT: C44.1, R_PD7.2, TMC5130.9, X_ENDSTOP.1
ENDSTOP_Y_LEFT: C47.1, R_PD8.2, TMC1.8, Y_ENDSTOP.5
ENDSTOP_Y_RIGHT: C46.1, R_PD9.2, TMC1.9, Y_ENDSTOP.1
ENDSTOP_Z_LEFT: C1.1, R_PD10.2, TMC2.8, Z_ENDSTOP.5
ENDSTOP_Z_RIGHT: C40.1, R_PD11.2, TMC2.9, Z_ENDSTOP.1
FAN: IC2.1, IC2.3, IC2.6, R28.1, SHIELD.9
GND: AUX-1.3, AUX-1.4, AUX-2.2, AUX-3.7, AUX-4.2, C2.1, C3.2, C4.2, C5.2, C6.2, C9.1, C10.1, C11.2, C12.1, C13.1, C14.1, C15.1, C18.1, C19.2, C20.1, C21.1, C22.2, C23.2, C26.1, C27.2, C28.1, C29.1, C30.2, C31.2, C34.1, C35.2, C36.1, C37.1, C38.2, C39.2, C41.2, C42.-, C43.-, D2.A, D4.A, D5.A, D6.A, E0_ENDSTOP.3, I2C.2, IC1.4, IC2.4, IC6.4, MAIN_IN.P$1, MAIN_IN.P$3, R5.1, R7.1, R10.1, R11.1, R13.1, R14.1, R16.1, R17.1, R27.2, R28.2, R29.2, RL2.1, RL3.1, R_PD6.1, R_PD7.1, R_PD8.1, R_PD9.1, R_PD10.1, R_PD11.1, R_PD12.1, R_PD13.1, S1.1, S1.2, SERV_SUPPLY.2, SERV_SUPPLY.4, SERV_SUPPLY.6, SERV_SUPPLY.8, SHIELD.GND@0, SHIELD.GND@1, SHIELD.GND@2, SHIELD.GND@3, SHIELD.GND@4, T1.S0, T1.S1, T1.S2, T2.S0, T2.S1, T2.S2, T3.S0, T3.S1, T3.S2, THERM0.1, THERM1.1, THERM2.1, TMC1.1, TMC1.6, TMC1.11, TMC1.13, TMC1.23, TMC1.31, TMC1.32, TMC1.36, TMC1.48, TMC1.PAD, TMC2.1, TMC2.6, TMC2.11, TMC2.13, TMC2.23, TMC2.31, TMC2.32, TMC2.36, TMC2.48, TMC2.PAD, TMC3.1, TMC3.6, TMC3.11, TMC3.13, TMC3.23, TMC3.31, TMC3.32, TMC3.36, TMC3.48, TMC3.PAD, TMC5130.1, TMC5130.6, TMC5130.11, TMC5130.13, TMC5130.23, TMC5130.31, TMC5130.32, TMC5130.36, TMC5130.48, TMC5130.PAD, VM0.1, VM1.1, XTAL.2, X_ENDSTOP.3, Y_ENDSTOP.3, Z_ENDSTOP.3
HEATBED: IC6.1, IC6.3, IC6.6, R27.1, SHIELD.8
HEATBED_POWER: F2.P$1, MAIN_IN.P$4
HEAT_E0: IC1.1, IC1.3, IC1.6, R29.1, SHIELD.10
INTERRUPT: R33.2, SHIELD.2, TMC1.26, TMC2.26, TMC3.26, TMC5130.26
M1A1_E0: E0_MOTOR.1, TMC3.46
M1A1_X: TMC5130.46, X_MOTOR.1
M1A1_Y: TMC1.46, Y_MOTOR.1
M1A1_Z: TMC2.46, Z_MOTOR_1.1
M1A2_E0: E0_MOTOR.2, TMC3.42
M1A2_X: TMC5130.42, X_MOTOR.2
M1A2_Y: TMC1.42, Y_MOTOR.2
M1A2_Z: TMC2.42, Z_MOTOR_2.2
M1B1_E0: E0_MOTOR.3, TMC3.15
M1B1_X: TMC5130.15, X_MOTOR.3
M1B1_Y: TMC1.15, Y_MOTOR.3
M1B1_Z: TMC2.15, Z_MOTOR_1.3
M1B2_E0: E0_MOTOR.4, TMC3.19
M1B2_X: TMC5130.19, X_MOTOR.4
M1B2_Y: TMC1.19, Y_MOTOR.4
M1B2_Z: TMC2.19, Z_MOTOR_2.4
MAIN_POWER: F1.P$1, MAIN_IN.P$2
MISO: AUX-3.3, SHIELD.50, TMC1.7, TMC2.7, TMC3.7, TMC5130.7
MOSI: AUX-3.4, SHIELD.51, TMC1.5, TMC2.5, TMC3.5, TMC5130.5
unnamed: Z_MOTOR_1.2, Z_MOTOR_2.1
unnamed: Z_MOTOR_1.4, Z_MOTOR_2.3
unnamed: C17.1, TMC1.37
unnamed: C17.2, TMC1.35
unnamed: C16.2, TMC1.38
unnamed: C6.1, R6.1, TMC5130.33
unnamed: C8.1, TMC5130.37
unnamed: C8.2, TMC5130.35
unnamed: C7.2, TMC5130.38
unnamed: C9.2, R6.2, TMC5130.34
unnamed: C21.2, R12.2, TMC1.34
unnamed: C4.1, R12.1, TMC1.33
unnamed: C25.1, TMC2.37
unnamed: C25.2, TMC2.35
unnamed: C24.2, TMC2.38
unnamed: C29.2, R15.2, TMC2.34
unnamed: C23.1, R15.1, TMC2.33
unnamed: C33.1, TMC3.37
unnamed: C33.2, TMC3.35
unnamed: C32.2, TMC3.38
unnamed: C37.2, R18.2, TMC3.34
unnamed: C31.1, R18.1, TMC3.33
unnamed: LED3.C, RL3.2
unnamed: LED2.C, RL2.2
unnamed: LED6.A, R24.1
unnamed: D_HB1.A, EX_0.P$1, LED1.C, T3.D0, T3.D1, T3.D2, T3.D3, T3.D4, T3.D5, T3.D6
unnamed: R4.1, R8.1, R9.1, T3.G
unnamed: IC1.7, R8.2
unnamed: IC1.5, R4.2
unnamed: IC1.2, R9.2
unnamed: LED1.A, R21.1
unnamed: D_HB2.A, FAN.P$1, LED4.C, T2.D0, T2.D1, T2.D2, T2.D3, T2.D4, T2.D5, T2.D6
unnamed: R22.1, R23.1, R25.1, T2.G
unnamed: D_HB.A, HEATBED.P$1, LED6.C, T1.D0, T1.D1, T1.D2, T1.D3, T1.D4, T1.D5, T1.D6
unnamed: R30.1, R31.1, R32.1, T1.G
unnamed: IC2.7, R23.2
unnamed: IC2.5, R22.2
unnamed: IC6.7, R31.2
unnamed: IC6.5, R30.2
unnamed: IC6.2, R32.2
unnamed: IC2.2, R25.2
unnamed: LED4.A, R26.1
POSPULSE: R34.2, SHIELD.3, TMC1.27, TMC2.27, TMC3.27, TMC5130.27
RESET: S1.3, S1.4, SHIELD.RESET
SCK: AUX-3.5, SHIELD.52, TMC1.4, TMC2.4, TMC3.4, TMC5130.4
SCL: I2C.4, R20.1, SHIELD.21
SDA: I2C.3, R19.1, SHIELD.20
SENSE1: R5.2, TMC5130.44
SENSE2: R7.2, TMC5130.17
SENSE3: R10.2, TMC1.17
SENSE4: R11.2, TMC1.44
SENSE5: R13.2, TMC2.17
SENSE6: R14.2, TMC2.44
SENSE7: R16.2, TMC3.17
SENSE8: R17.2, TMC3.44
THERM0: C12.2, R1.1, SHIELD.A13, THERM0.2
THERM1: C13.2, R2.1, SHIELD.A14, THERM1.2
THERM2: C14.2, R3.1, SHIELD.A15, THERM2.2
VM: C7.1, C10.2, C11.1, C15.2, C16.1, C18.2, C19.1, C20.2, C24.1, C26.2, C27.1, C28.2, C32.1, C34.2, C35.1, C36.2, C43.+, D2.C, D4.C, D5.C, D6.C, D_HB1.C, D_HB2.C, EX_0.P$2, F1.P$2, FAN.P$2, LED3.A, R21.2, R26.2, TMC1.21, TMC1.39, TMC1.40, TMC2.21, TMC2.39, TMC2.40, TMC3.21, TMC3.39, TMC3.40, TMC5130.21, TMC5130.39, TMC5130.40, VM0.2, VM1.2
V_HEATBED: C42.+, D_HB.C, F2.P$2, HEATBED.P$2, LED2.A, R24.2

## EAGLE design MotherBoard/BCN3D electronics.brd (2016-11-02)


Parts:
+5V, +24V: JP2Q
ADC: M04PTH; 1X04
ATMEGA2560: ATMEGA2560-16AU; QFP50P1600X1600X120-100N
C1, C2: 22p; C0805; MPN 08055A220KAT2A
C3, C4, C5, C6, C10, C19, C20, C21, C24: 100n; C0805; MPN 08055C104KAT2A
C7: 150UF; CAPAE660X610N; MPN EEEFP1A151AP
C8: 220u; UD-8X10_NICHICON; MPN EEE1VA221UAP
C9, C11, C15: 10u; C0805; MPN 08055C104KAT2A
C12, C13: 100u; UD-8X10_NICHICON; MPN EEEFC1V101AP
C14, C16: 10u; C1210K; MPN GRM32ER7YA106KA12L
C17: 4.7u; C0805; MPN 06035C103JAT2A
C18, C25: 10n; C0805; MPN 08055C103KAT2A
C22, C23: 0.1u; C0805; MPN 08055C104KAT2A
D1: SCHOTTKY-DIODESMC; SMC; MPN MBRS340T3G
D2, D3, D4, D5, D6, D7, D9: MBRA140; SMA-DIODE; MPN B140-13-F
D8, D10: MBR0520LT; SOD123; MPN DA22F2100L
E0, E1: FFC_15V_90G_1MM; TE_FFC_CON1MM
F1: IN_PTC; PTC-1206; MPN 3413.0329.22
F3: MICROBUILDER_PTC1206_L; MICROBUILDER_1206_PTC; MPN 1206L050YR
FID1, FID2, FID3: FIDUCIAL; FIDUCIAL_1MM
HEATEDBED: PC4WAY; MOLEX_MINIFIT-JR; MPN 39303045
HOTEND0, HOTEND1: 68612014422
I2C: M04PTH; 1X04
IC1: LM358D; SO08; MPN LM2904DT
IC2: FT232RL; SSOP28
IC3: LM311D; SO08
ICSP: AVR_SPI_PRG_6NS; 2X3-NS
K1: G5L; G5LE; MPN G5LA-1 5DC
L1: 100u; SSR1260; MPN SRR1260-101M
L2, L3, L4, L5, L6, L7, L8, L9, L10, L11, L12, L13, L14, L15, L16, L17, L18, L19, L20, L21: WE-CBF_0805; 0805
LCD: PINHD-1X6; 1X06
LED1, LED2, LED3: Blue; CHIPLED_0805; MPN OVS-0803
LEDS1: M04PTH; 1X04
LM2595: LM2595; TO263-5; MPN LM2595S-5.0/NOPB
LOGO1: OSHW-LOGOM; OSHW-LOGO-M
PWR5, PWR24: Blue; CHIPLED_0805; MPN OVS-0803
Q1, Q2, Q3: MOSFET-NSOIC8; SOIC8; MPN IRF8736PBF
Q4, Q5, Q9: MMBT2222A; SOT23-3; MPN BC817-40
Q6, Q7, Q8: MOSFET-NREFLOW; SOT23; MPN BSH103,215
R1, R18, R31, R40, R42: 10K; M0805; MPN CR0805-JW-102ELF
R2, R8, R11: 5.6k; M0805; MPN CR0805-JW-102ELF
R3, R39: 1K; R0805; MPN CR0805-JW-102ELF
R4, R5: 4.7k; M0805; MPN CR0805-JW-103ELF
R6, R9, R12, R14, R15, R19, R20, R21, R22, R27, R30, R33, R34, R35, R36, R43: 1K; M0805; MPN CR0805-JW-102ELF
R7, R10, R13: 10K; M0805; MPN CR0805-JW-103ELF
R16, R17, R26, R28, R29: 4.7K; M0805; MPN CR0805-FX-4701GLF
R23, R24, R25: VARISTORCN0805; CT/CN0805; MPN V5.5MLA0805LH
R32: 330; M0805; MPN CR0805-JW-103ELF
R37: 10k; M0805; MPN CR0805-JW-103ELF
R38: 5.6K; R0805; MPN CR0805-FX-4701GLF
R41: 20K; M0805; MPN CR0805-FX-4701GLF
R44: 100K; M0805; MPN CR0805-JW-102ELF
R45, R46, R47: 1K; M0805; MPN CR0805-FX-4701GLF
RESET: SPST; EVQ-Q2; MPN EVQQ2503W
RGBLEDS: M04PTH; 1X04
RSHUNT: 10m; R2512
RXLED: green; CHIPLED_0805; MPN 150080VS75000
SD: PINHD-1X6; 1X06
SH1: SHORTT5; SHORT_TOP-50
SJ1: SJ
STAT: Orange; CHIP-LED0805; MPN KP-2012SECK
SUPPLY: PC4WAY; MOLEX_MINIFIT-JR; MPN 39303045
TP1, TP2, TP3, TP4, TP5, TP7, TP8, TP9, TP10, TP11, TP12, TP13, TP15, TP16, TP17, TP19, TP20, TP21, TP22, TP23, TP24, TP25, TP26, TP27, TP28, TP29, TP30, TP31, TP32, TP33, TP34, TP35, TP36, TP37, TP38: TPB2,54; B2,54
TXLED: green; CHIPLED_0805; MPN 150080VS75000
U1: INA169; SOT23-5
U$6: USB+SHIELD; USB-B-PTH; MPN 67068-8000
UART1: M04PTH; 1X04
VCC2: JP1E; JP1
X0, X1: FFC_15V_90G_1MM; TE_FFC_CON1MM
Y0: FFC_15V_90G_1MM; TE_FFC_CON1MM
Y1: CRYSTALHC49US; HC49US; MPN 9B-16.000MAAJ-B
Z: FFC_15V_90G_1MM; TE_FFC_CON1MM

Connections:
24VBF: F1.1, RSHUNT.2, U1.4 (VIN-)
24VINA: K1.P, RSHUNT.1, U1.3 (VIN+)
!RESET: ATMEGA2560.30 (~RESET), C19.2, C25.1, D10.A, ICSP.5, R32.1, R37.1
+5V: +24V.1, +24V.3, ATMEGA2560.10 (VCC_3), ATMEGA2560.31 (VCC_2), ATMEGA2560.61 (VCC_4), ATMEGA2560.80 (VCC), ATMEGA2560.100 (AVCC), C3.1, C4.1, C5.1, C7.1, C10.1, C17.1, C18.1, C21.1, C24.1, D4.C, D8.C, D10.C, E0.12, E0.14, E1.12, E1.14, HOTEND0.1, HOTEND1.1, I2C.1, IC1.8 (V+), IC2.4 (VCCIO), IC2.19 (!RESET), IC2.20 (VCC), IC3.8 (V+), ICSP.2, K1.1, L1.B (2), LCD.1, LM2595.4 (FB), PWR5.A, R1.1, R4.1, R5.1, R16.2, R17.2, R26.2, R28.2, R29.2, R33.2, R34.2, R37.2, R43.1, SD.6, TP3.TP, U1.5 (V+), UART1.1, X0.12, X0.14, X1.12, X1.14, Y0.12, Y0.14, Z.12, Z.14
+24V: D3.C, D5.C, D6.C, D7.C, D9.C, E0.1, E0.3, E0.5, E1.1, E1.3, E1.5, F1.2, HEATEDBED.1, HOTEND0.8, HOTEND0.10, HOTEND0.12, HOTEND0.18, HOTEND0.19, HOTEND1.8, HOTEND1.10, HOTEND1.12, HOTEND1.18, HOTEND1.19, LED1.A, LED2.A, LED3.A, X0.1, X0.3, X0.5, X1.1, X1.3, X1.5, Y0.1, Y0.3, Y0.5, Y0.GND@2 (GND), Z.1, Z.3, Z.5
ADC10: ADC.1, ATMEGA2560.87 (PK2_(ADC10/PCINT18))
ADC11: ADC.2, ATMEGA2560.86 (PK3_(ADC11/PCINT19))
ADC12: ADC.3, ATMEGA2560.85 (PK4_(ADC12/PCINT20))
ADC13: ADC.4, ATMEGA2560.84 (PK5_(ADC13/PCINT21))
B-PWM: ATMEGA2560.26 ((OC0A/OC1C/PCINT7)_PB7), R22.2
BED_THERM: ATMEGA2560.82 (PK7_(ADC15/PCINT23)), R45.2
BED_THERM_CON: C15.1, HEATEDBED.3, R28.1, R45.1, TP13.TP
E0-!EN: ATMEGA2560.72 (PA6_(AD6)), L7.1, TP34.TP
E0-DIR: ATMEGA2560.73 (PA5_(AD5)), L8.1, TP33.TP
E0-STEP: ATMEGA2560.71 (PA7_(AD7)), L6.1, TP35.TP
E0-STOP: ATMEGA2560.74 (PA4_(AD4)), E0.11
E1-!EN: ATMEGA2560.95 (PF2_(ADC2)), L10.2, TP31.TP
E1-DIR: ATMEGA2560.96 (PF1_(ADC1)), L11.2, TP32.TP
E1-STEP: ATMEGA2560.94 (PF3_(ADC3)), L9.2, TP30.TP
E1-STOP: ATMEGA2560.97 (PF0_(ADC0)), E1.11
EARTH: L21.2, U$6.S1, U$6.S2
G-PWM: ATMEGA2560.24 ((OC1A/PCINT5)_PB5), R20.2
GND: +5V.2, +5V.4, +24V.2, +24V.4, ATMEGA2560.11 (GND_2), ATMEGA2560.32 (GND_4), ATMEGA2560.62 (GND_3), ATMEGA2560.81 (GND_5), ATMEGA2560.99 (GND), C3.2, C4.2, C5.2, C6.2, C7.2, C8.-, C9.2, C10.2, C11.2, C12.-, C13.-, C14.2, C15.2, C16.2, C17.2, C18.2, C20.2, C21.2, C22.2, C23.2, C24.2, C25.2, D1.A, E0.2, E0.4, E0.8, E0.10, E0.13, E0.15, E0.GND@1 (GND), E0.GND@2 (GND), E1.2, E1.4, E1.8, E1.10, E1.13, E1.15, E1.GND@1 (GND), E1.GND@2 (GND), HEATEDBED.2, HOTEND0.2, HOTEND0.4, HOTEND0.7, HOTEND0.9, HOTEND0.11, HOTEND0.17, HOTEND1.2, HOTEND1.4, HOTEND1.7, HOTEND1.9, HOTEND1.11, HOTEND1.17, I2C.2, IC1.4 (V-), IC2.7 (GND), IC2.18 (GND), IC2.21 (GND), IC2.25 (GND), IC2.26 (TEST), IC3.1 (GND), IC3.4 (V-), ICSP.6, L21.1, LCD.4, LCD.6, LM2595.3 (GND), LM2595.5 (EN), LM2595.6 (GND), Q1.1 (S), Q1.2 (S), Q1.3 (S), Q2.1 (S), Q2.2 (S), Q2.3 (S), Q3.1 (S), Q3.2 (S), Q3.3 (S), Q4.2 (E), Q5.2 (E), Q6.2 (S), Q7.2 (S), Q8.2 (S), Q9.2 (E), R7.2, R10.2, R13.2, R18.2, R23.2, R24.2, R25.2, R31.2, R38.1, R39.1, R40.2, R41.1, R42.2, RESET.A, RESET.A' (P1), SD.1, SH1.1, STAT.C, SUPPLY.2, SUPPLY.4, TP1.TP, U1.2 (GND), U$6.GND, UART1.2, X0.2, X0.4, X0.8, X0.10, X0.13, X0.15, X0.GND@1 (GND), X0.GND@2 (GND), X1.2, X1.4, X1.8, X1.10, X1.13, X1.15, X1.GND@1 (GND), X1.GND@2 (GND), Y0.2, Y0.4, Y0.8, Y0.10, Y0.13, Y0.15, Y0.GND@1 (GND), Z.2, Z.4, Z.8, Z.10, Z.13, Z.15, Z.GND@1 (GND), Z.GND@2 (GND)
GUARD: C1.2, C2.2, SH1.2
HOTBED: D3.A, HEATEDBED.4, Q1.5 (D), Q1.6 (D), Q1.7 (D), Q1.8 (D), R2.1
HOTEND0: D5.A, HOTEND0.13, HOTEND0.14, HOTEND0.15, HOTEND0.16, Q2.5 (D), Q2.6 (D), Q2.7 (D), Q2.8 (D), R8.1, TP7.TP
HOTEND0_THERM: ATMEGA2560.88 (PK1_(ADC9/PCINT17)), R46.2
HOTEND0_THERM_CON: C9.1, HOTEND0.3, R16.1, R46.1, TP12.TP
HOTEND1: D6.A, HOTEND1.13, HOTEND1.14, HOTEND1.15, HOTEND1.16, Q3.5 (D), Q3.6 (D), Q3.7 (D), Q3.8 (D), R11.1, TP8.TP
HOTEND1_THERM: ATMEGA2560.89 (PK0_(ADC8/PCINT16)), R47.2
HOTEND1_THERM_CON: C11.1, HOTEND1.3, R17.1, R47.1, TP11.TP
INA_OUT: IC3.3 (-IN), R41.2, U1.1 (OUT)
LCDRESET: ATMEGA2560.18 ((OC2B)_PH6), LCD.5, TP4.TP
LCDRX: ATMEGA2560.13 ((TXD2)_PH1), LCD.3, TP5.TP
LCDTX: ATMEGA2560.12 ((RXD2)_PH0), LCD.2, TP15.TP
LFAN0: D7.A, HOTEND0.5, HOTEND0.6, Q4.3 (C), TP9.TP
LFAN1: D9.A, HOTEND1.5, HOTEND1.6, Q5.3 (C), TP10.TP
LMIN: C8.+, D2.C, LM2595.2 (IN)
MISO: ATMEGA2560.22 ((MISO/PCINT3)_PB3), ICSP.1, SD.2, TP20.TP
MLED: ATMEGA2560.83 (PK6_(ADC14/PCINT22)), IC1.3 (+IN)
MOSI: ATMEGA2560.21 ((MOSI/PCINT2)_PB2), ICSP.4, SD.4, TP17.TP
unnamed: C19.1, IC2.2 (!DTR)
unnamed: ATMEGA2560.98 (AREF), C6.1
unnamed: L12.1, X0.6
unnamed: IC2.23 (CBUS0), TXLED.C
unnamed: IC2.22 (CBUS1), RXLED.C
unnamed: LEDS1.2, Q6.3 (D), RGBLEDS.2
unnamed: LEDS1.3, Q7.3 (D), RGBLEDS.3
unnamed: LEDS1.4, Q8.3 (D), RGBLEDS.4
unnamed: R32.2, RESET.B (S), RESET.B' (S1)
unnamed: D8.A, L2.2
unnamed: IC1.1 (OUT), IC1.2 (-IN), R3.2
unnamed: Q6.1 (G), R18.1, R20.1
unnamed: R3.1, STAT.A
unnamed: Q7.1 (G), R21.1, R31.1
unnamed: Q8.1 (G), R22.1, R40.1
unnamed: L13.1, X0.7
unnamed: L14.1, X0.9
unnamed: L18.1, Y0.6
unnamed: L19.1, Y0.7
unnamed: L20.1, Y0.9
unnamed: L15.1, X1.6
unnamed: L16.1, X1.7
unnamed: L17.1, X1.9
unnamed: E0.6, L6.2
unnamed: E0.7, L7.2
unnamed: E0.9, L8.2
unnamed: F3.2, L2.1
unnamed: IC3.2 (+IN), R1.2, R42.1, R44.1
unnamed: L3.1, Z.6
unnamed: L4.1, Z.7
unnamed: L5.1, Z.9
unnamed: E1.9, L11.1
unnamed: E1.7, L10.1
unnamed: E1.6, L9.1
unnamed: LED1.C, R2.2
unnamed: Q1.4 (G), R6.1, R7.1
unnamed: C20.1, IC2.17 (3V3OUT)
unnamed: R33.1, TXLED.A
unnamed: R34.1, RXLED.A
unnamed: Q4.1 (B), R14.1
unnamed: LED2.C, R8.2
unnamed: Q2.4 (G), R9.1, R10.1
unnamed: D4.A, K1.2, Q9.3 (C)
unnamed: LED3.C, R11.2
unnamed: Q3.4 (G), R12.1, R13.1
unnamed: Q5.1 (B), R15.1
unnamed: PWR24.C, R38.2
unnamed: PWR5.C, R39.2
OUT: D1.C, L1.A (1), LM2595.1 (OUT)
PWM_HOTBED: ATMEGA2560.38 ((OC5A)_PL3), R6.2
PWM_HOTEND0: ATMEGA2560.40 (OC5C)_PL5), R9.2
PWM_HOTEND1: ATMEGA2560.16 ((OC4B)_PH4), R12.2
PWM_LFAN0: ATMEGA2560.39 ((OC5B)_PL4), R14.2
PWM_LFAN1: ATMEGA2560.15 ((OC4A)_PH3), R15.2
R-PWM: ATMEGA2560.25 ((OC1B/PCINT6)_PB6), R21.2
RELAY: ATMEGA2560.23 ((OC2A/PCINT4)_PB4), R19.2
RELAYINA: IC3.7 (OUT), Q9.1 (B), R19.1, R43.2, R44.2, SJ1.1, SJ1.2
RX: IC2.1 (TXD), R35.2
RX1: ATMEGA2560.45 ((RXD1/INT2)_PD2), UART1.3
SCL: ATMEGA2560.43 ((SCL/INT0)_PD0), I2C.3, R4.2
SCLK: ATMEGA2560.20 ((SCK/PCINT1)_PB1), ICSP.3, SD.3, TP19.TP
SDA: ATMEGA2560.44 ((SDA/INT1)_PD1), I2C.4, R5.2
SDSS: ATMEGA2560.19 ((~SS/PCINT0)_PB0), SD.5, TP16.TP
SUPPLY: C12.+, C13.+, C14.1, C16.1, K1.S, LEDS1.1, PWR24.A, RGBLEDS.1, SUPPLY.1, SUPPLY.3, TP2.TP, VCC2.1
TX: IC2.5 (RXD), R36.2
TX1: ATMEGA2560.46 ((TXD1/INT3)_PD3), UART1.4
UART_N: ATMEGA2560.3 ((TXD0)_PE1), R36.1
UART_P: ATMEGA2560.2 ((RXD0/PCINT8)_PE0), R35.1
USBD+_P: IC2.15 (USBDP), R23.1, U$6.D+
USBD-_N: IC2.16 (USBDM), R24.1, U$6.D-
VBUS: F3.1, R25.1, U$6.VBUS
VCC2: +5V.1, +5V.3, D2.A, VCC2.2
X0-!EN: ATMEGA2560.67 (PJ4_(PCINT13)), L13.2, TP22.TP
X0-DIR: ATMEGA2560.68 (PJ5_(PCINT14)), L14.2, TP23.TP
X0-STEP: ATMEGA2560.66 (PJ3_(PCINT12)), L12.2, TP21.TP
X0-STOP: ATMEGA2560.69 (PJ6_(PCINT15)), X0.11
X1-!EN: ATMEGA2560.6 ((OC3B/INT4)_PE4), L16.2, TP25.TP
X1-DIR: ATMEGA2560.7 ((OC3C/INT5)_PE5), L17.2, TP26.TP
X1-STEP: ATMEGA2560.5 ((OC3A/AIN1)_PE3), L15.2, TP24.TP
X1-STOP: ATMEGA2560.8 ((T3/INT6)_PE6), X1.11
XTAL_N: ATMEGA2560.33 (XTAL2), C1.1, Y1.2
XTAL_P: ATMEGA2560.34 (XTAL1), C2.1, Y1.1
Y-!EN: ATMEGA2560.59 (PC6_(A14)), L19.2, TP28.TP
Y-DIR: ATMEGA2560.58 (PC5_(A13)), L20.2, TP29.TP
Y-STEP: ATMEGA2560.60 (PC7_(A15)), L18.2, TP27.TP
Y-STOP: ATMEGA2560.57 (PC4_(A12)), Y0.11
Z0-ENDSTOP: HOTEND0.20, R26.1, R27.1
Z0-STOP: ATMEGA2560.56 (PC3_(A11)), C22.1, R27.2
Z1-ENDSTOP: HOTEND1.20, R29.1, R30.1
Z1-STOP: ATMEGA2560.41 (PL6), C23.1, R30.2
Z-!EN: ATMEGA2560.76 (PA2_(AD2)), L4.2, TP37.TP
Z-DIR: ATMEGA2560.77 (PA1_(AD1)), L5.2, TP36.TP
Z-STEP: ATMEGA2560.75 (PA3_(AD3)), L3.2, TP38.TP
Z-STOP: Z.11

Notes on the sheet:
Power Output
Thermistors
USB COMUNICATION
ATmega2560
Power in to 5V
Power Supply
Display
TEST POINTS
FIDUCIALS
SD card Module
Extension Pin Header
4D Systems Display. Communication through serial.
BCN3D - Barcelona 2014 Marc Cobler Cosmen www.bcn3dtechnologies.com www.fundaciocim.org
Design based on the Megatronics V3.0 and SAV mkI. Released under the CERN Open Hardware License
Integrated electronics for controlled numeric Machines.
Stepper outputs
The stepper drivers are integrated on the back of each stepper motor to improve EMC performance.
BCN3D electronics MainBoard
RGB LEDs
Analog RGB LED strip - 4 PWM outputs needed
VCC2 (24V) it's only for the DC/DC Converter and the LED's
Z-Endstops
CSM - Current Shunt Monitor
INA169 monitors current on the high side and acts on the relay. 0.2 Volt per Amp
CSM



Board: 2 copper layers, 80.0 x 140.0 mm, 201 parts (41 on the bottom side), 134 nets.

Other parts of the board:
U$2: TONNE_10.00
U$3: FCC_10X4.175MM
U$4: CE-4MM
U$5, U$8: BCN3D_LOGO
U$9: FCIM_LOGO

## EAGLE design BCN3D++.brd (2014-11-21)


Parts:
24V: PTR1TP12SQ; TP12SQ
+5V: PTR1TP12SQ; TP12SQ
+24V: control; SCREWTERMINAL-5MM-2
+24V1: HEATED BED; SCREWTERMINAL-5MM-2
ALVL: PINHD-1X2; 1X02
ATMEGA2560: ATMEGA2560-16AU; QFP50P1600X1600X120-100N
C1, C2: 22p; C0805
C3, C4, C5, C6, C20: 100n; C0805
C7: 4.7u; C1206K
C8: 220u; UD-8X10_NICHICON
C9, C15: 0.1u; C0805
C21: 10n; C0805K
CARRIAGE0, CARRIAGE1, CARRIAGE2, CARRIAGE3: M06SIP; 1X06
D1: MBRS140; DO-214AA
D3, D8: MBR0520LT; SOD123
D9: CGRM4004-G; SOD-123_MINI-SMA
E0-AXIS, E1-AXIS, E2-AXIS, E3-AXIS: M06SIP; 1X06
ENDSTOPS: PINCONNECTOR-7X3; MALE-PIN-3X7
F1: PTCSMD; PTC-1206
FANS: JP4QE; JP4Q
FID1, FID2, FID3: FIDUCIAL; FIDUCIAL_1MM
GND: PTR1TP12SQ; TP12SQ
HOTBED: M025MM; SCREWTERMINAL-5MM-2
IC2: FT232RL; SSOP28
ICSP: AVR_SPI_PRG_6NS; 2X3-NS
L1: 100u; SSR1260
L2, L4: WUERTH-ELEKTRONIK_WE-CBF_1206W; WUERTH-ELEKTRONIK_1206W
LCD: M06SIP; 1X06
LED2: HOTBED; CHIP-LED0603
LM2595: LM2596S; TO263-5
LOGO1: OSHW-LOGOM; OSHW-LOGO-M
PRW5: Red; CHIP-LED0805
PTC1: MICROBUILDER_PTC1206_L; MICROBUILDER_1206_PTC
PWR24: Red; CHIP-LED0805
Q2: IRLS3034; D2PACK
Q6, Q7, Q8: MOSFET-NREFLOW; SOT23
R1: 1M; R0805
R2, R28: 4.7K; M0805
R16, R19, R33, R34, R35, R36: 1K; M0805
R17: 10K; M0805
R37: 10k; M0805
R38: 4.7K; R0805
R39: 1K; R0805
RESET: SWITCHSMD; TACTILE-SWITCH-SMD
RGBLEDS: M04PTH; 1X04
RXLED: green; CHIP-LED0603
SD: M06SIP; 1X06
THERM: PINHD-1X2; 1X02
TXLED: green; CHIP-LED0603
U$1, U$2, U$3, U$4: SANGUINOLOLU_PLATED-SCREW; SANGUINOLOLU_PLATEDSCREW
USB: MINI-USB-SCHIELD; 32005-201
X0-AXIS, X1-AXIS, X2-AXIS, X3-AXIS: M06SIP; 1X06
Y0-AXIS, Y1-AXIS: M06SIP; 1X06
Y1: CRYSTALHC49US; HC49US
Z-AXIS: M06SIP; 1X06

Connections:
11111: ATMEGA2560.23 ((OC2A/PCINT4)_PB4)
!RESET: ATMEGA2560.30 (~RESET), ICSP.5, R37.1, RESET.1, RESET.2
+5V: +5V.TP, ATMEGA2560.10 (VCC_3), ATMEGA2560.31 (VCC_2), ATMEGA2560.61 (VCC_4), ATMEGA2560.80 (VCC), ATMEGA2560.100 (AVCC), C3.1, C4.1, C5.1, C8.+, CARRIAGE0.4, CARRIAGE1.4, CARRIAGE2.4, CARRIAGE3.4, D8.C, E0-AXIS.3, E1-AXIS.3, E2-AXIS.3, E3-AXIS.3, ENDSTOPS.15 (3), ENDSTOPS.16 (3), ENDSTOPS.17 (3), ENDSTOPS.18 (3), ENDSTOPS.19 (3), ENDSTOPS.20 (3), ENDSTOPS.21 (3), FANS.5 (1), FANS.7 (1), IC2.4 (VCCIO), IC2.19 (!RESET), IC2.20 (VCC), ICSP.2, L1.B (2), LCD.5, LM2595.4 (FB), PRW5.A, R2.2, R28.2, R33.2, R34.2, R37.2, SD.6, X0-AXIS.3, X1-AXIS.3, X2-AXIS.3, X3-AXIS.3, Y0-AXIS.3, Y1-AXIS.3, Z-AXIS.3
+24V: 24V.TP, C7.1, CARRIAGE0.6, CARRIAGE1.6, CARRIAGE2.6, CARRIAGE3.6, D3.C, D9.C, E0-AXIS.1, E1-AXIS.1, E2-AXIS.1, E3-AXIS.1, F1.2, FANS.1, FANS.3 (1), HOTBED.1, LED2.A, LM2595.1 (IN), PWR24.A, RGBLEDS.1, X0-AXIS.1, X1-AXIS.1, X2-AXIS.1, X3-AXIS.1, Y0-AXIS.1, Y1-AXIS.1, Z-AXIS.1
AUTO_LEVEL: ALVL.1, ATMEGA2560.84 (PK5_(ADC13/PCINT21)), C9.1, R2.1
B-PWM: ATMEGA2560.26 ((OC0A/OC1C/PCINT7)_PB7), Q8.1 (G)
BED_THERM: ATMEGA2560.89 (PK0_(ADC8/PCINT16)), C15.1, R28.1, THERM.1
E0-!EN: ATMEGA2560.76 (PA2_(AD2)), E0-AXIS.4
E1-!EN: ATMEGA2560.75 (PA3_(AD3)), E1-AXIS.4
E2-!EN: ATMEGA2560.74 (PA4_(AD4)), E2-AXIS.4
E3-!EN: ATMEGA2560.73 (PA5_(AD5)), E3-AXIS.4
E-DIR: ATMEGA2560.77 (PA1_(AD1)), E0-AXIS.5, E1-AXIS.5, E2-AXIS.5, E3-AXIS.5
E-STEP: ATMEGA2560.78 (PA0_(AD0)), E0-AXIS.6, E1-AXIS.6, E2-AXIS.6, E3-AXIS.6
G-PWM: ATMEGA2560.24 ((OC1A/PCINT5)_PB5), Q6.1 (G)
GND: +24V.2, +24V1.2, ALVL.2, ATMEGA2560.11 (GND_2), ATMEGA2560.32 (GND_4), ATMEGA2560.62 (GND_3), ATMEGA2560.81 (GND_5), ATMEGA2560.99 (GND), C1.2, C2.2, C3.2, C4.2, C5.2, C6.2, C7.2, C8.-, C9.2, C15.2, C20.2, C21.2, CARRIAGE0.5, CARRIAGE1.5, CARRIAGE2.5, CARRIAGE3.5, D1.A, D9.A, E0-AXIS.2, E1-AXIS.2, E2-AXIS.2, E3-AXIS.2, ENDSTOPS.8 (2), ENDSTOPS.9 (2), ENDSTOPS.10 (2), ENDSTOPS.11 (2), ENDSTOPS.12 (2), ENDSTOPS.13 (2), ENDSTOPS.14 (2), FANS.2, FANS.4 (2), FANS.6 (2), FANS.8 (2), GND.TP, IC2.7 (GND), IC2.18 (GND), IC2.21 (GND), IC2.25 (GND), IC2.26 (TEST), ICSP.6, L4.2, LCD.4, LM2595.3 (GND), LM2595.5 (EN), LM2595.6 (GND), Q2.3 (S), Q6.2 (S), Q7.2 (S), Q8.2 (S), R17.2, R38.1, R39.1, RESET.3, RESET.4, SD.5, THERM.2, U$1.GND, U$2.GND, U$3.GND, U$4.GND, X0-AXIS.2, X1-AXIS.2, X2-AXIS.2, X3-AXIS.2, Y0-AXIS.2, Y1-AXIS.2, Z-AXIS.2
HOTEND0: ATMEGA2560.18 ((OC2B)_PH6), CARRIAGE0.2
HOTEND1: ATMEGA2560.16 ((OC4B)_PH4), CARRIAGE1.2
HOTEND2: CARRIAGE2.2
HOTEND3: CARRIAGE3.2
LCDRESET: ATMEGA2560.47 ((ICP1)_PD4), LCD.1
LCDRX: ATMEGA2560.46 ((TXD1/INT3)_PD3), LCD.2
LCDTX: ATMEGA2560.45 ((RXD1/INT2)_PD2), LCD.3
LFAN0: ATMEGA2560.17 ((OC4C)_PH5), CARRIAGE0.3
LFAN1: ATMEGA2560.15 ((OC4A)_PH3), CARRIAGE1.3
LFAN2: CARRIAGE2.3
LFAN3: CARRIAGE3.3
MISO: ATMEGA2560.22 ((MISO/PCINT3)_PB3), ICSP.1, SD.3
MOSI: ATMEGA2560.21 ((MOSI/PCINT2)_PB2), ICSP.4, SD.2
unnamed: ATMEGA2560.33 (XTAL2), C1.1, R1.2, Y1.2
unnamed: ATMEGA2560.98 (AREF), C6.1
unnamed: ATMEGA2560.34 (XTAL1), C2.1, R1.1, Y1.1
unnamed: D1.C, L1.A (1), LM2595.2 (OUT)
unnamed: C21.1, L2.2, PTC1.2
unnamed: IC2.23 (CBUS0), TXLED.C
unnamed: IC2.22 (CBUS1), RXLED.C
unnamed: Q6.3 (D), RGBLEDS.2
unnamed: Q7.3 (D), RGBLEDS.3
unnamed: Q8.3 (D), RGBLEDS.4
unnamed: +24V.1, +24V1.1, F1.1
unnamed: Q2.1 (G), R16.1, R17.1
unnamed: D3.A, HOTBED.2, Q2.2 (D), R19.1
unnamed: LED2.C, R19.2
unnamed: C20.1, IC2.17 (3V3OUT)
unnamed: R33.1, TXLED.A
unnamed: R34.1, RXLED.A
unnamed: D8.A, L2.1
unnamed: PTC1.1, USB.1
unnamed: PWR24.C, R38.2
unnamed: PRW5.C, R39.2
PWM_HOTBED: ATMEGA2560.1 ((OC0B)_PG5), R16.2
R-PWM: ATMEGA2560.25 ((OC1B/PCINT6)_PB6), Q7.1 (G)
RX: IC2.1 (TXD), R35.2
RX0: ATMEGA2560.2 ((RXD0/PCINT8)_PE0), R35.1
SCL: ATMEGA2560.43 ((SCL/INT0)_PD0)
SCLK: ATMEGA2560.20 ((SCK/PCINT1)_PB1), ICSP.3, SD.4
SDA: ATMEGA2560.44 ((SDA/INT1)_PD1)
SDSS: ATMEGA2560.19 ((~SS/PCINT0)_PB0), SD.1
THERM0: ATMEGA2560.87 (PK2_(ADC10/PCINT18)), CARRIAGE0.1
THERM1: ATMEGA2560.88 (PK1_(ADC9/PCINT17)), CARRIAGE1.1
THERM2: ATMEGA2560.86 (PK3_(ADC11/PCINT19)), CARRIAGE2.1
THERM3: ATMEGA2560.85 (PK4_(ADC12/PCINT20)), CARRIAGE3.1
TX: IC2.5 (RXD), R36.2
TX0: ATMEGA2560.3 ((TXD0)_PE1), R36.1
USBD+: IC2.15 (USBDP), USB.3
USBD-: IC2.16 (USBDM), USB.2
USBSHIELD: L4.1, USB.5, USB.M1 (S1), USB.M2 (S2), USB.M3 (S3), USB.M4 (S4)
X0-!EN: ATMEGA2560.94 (PF3_(ADC3)), X0-AXIS.4
X0-STOP: ATMEGA2560.63 (PJ0_(RXD3/PCINT9)), ENDSTOPS.1
X1-!EN: ATMEGA2560.93 (PF4_(ADC4/TCK)), X1-AXIS.4
X1-STOP: ATMEGA2560.64 (PJ1_(TXD3/PCINT10)), ENDSTOPS.2 (1)
X2-!EN: ATMEGA2560.92 (PF5_(ADC5/TMS)), X2-AXIS.4
X2-STOP: ATMEGA2560.67 (PJ4_(PCINT13)), ENDSTOPS.5 (1)
X3-!EN: ATMEGA2560.91 (PF6_(ADC6/TDO)), X3-AXIS.4
X3-STOP: ATMEGA2560.68 (PJ5_(PCINT14)), ENDSTOPS.6 (1)
X-DIR: ATMEGA2560.95 (PF2_(ADC2)), X0-AXIS.5, X1-AXIS.5, X2-AXIS.5, X3-AXIS.5
X-STEP: ATMEGA2560.96 (PF1_(ADC1)), X0-AXIS.6, X1-AXIS.6, X2-AXIS.6, X3-AXIS.6
Y0-!EN: ATMEGA2560.6 ((OC3B/INT4)_PE4), Y0-AXIS.4
Y0-STOP: ATMEGA2560.65 (PJ2_(XCK3/PCINT11)), ENDSTOPS.3 (1)
Y1-!EN: ATMEGA2560.7 ((OC3C/INT5)_PE5), Y1-AXIS.4
Y1-STOP: ATMEGA2560.66 (PJ3_(PCINT12)), ENDSTOPS.4 (1)
Y-DIR: ATMEGA2560.5 ((OC3A/AIN1)_PE3), Y0-AXIS.5, Y1-AXIS.5
Y-STEP: ATMEGA2560.90 (PF7_(ADC7/TDI)), Y0-AXIS.6, Y1-AXIS.6
Z-!EN: ATMEGA2560.97 (PF0_(ADC0)), Z-AXIS.4
Z-DIR: ATMEGA2560.71 (PA7_(AD7)), Z-AXIS.5
Z-STEP: ATMEGA2560.72 (PA6_(AD6)), Z-AXIS.6
Z-STOP: ATMEGA2560.69 (PJ6_(PCINT15)), ENDSTOPS.7 (1)

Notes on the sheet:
Endstops
Power Output
Thermistors
USB COMUNICATION
ATmega2560
Power in to 5V
Power Supply
Display
TEST POINTS
FIDUCIALS
SD card Module
Extension Pin Header
4D Systems Display. Communication through serial.
RepRapBCN - Barcelona 2014 Marc Cobler Cosmen www.reprapbcn.com
Design based on the Megatronics V3.0 and SAV mkI. Released under the Creative Commons Attribution Share-Alike 3.0 License
Integrated 3D printer electronics for RepRap Machines.
Stepper outputs
The stepper drivers are integrated on the back of each stepper motor to improve EMC performance.
BCN3D++ Mother Board
RGB LEDs
Analog RGB LED strip - 3 PWM outputs needed Normally strips go to 12V but we have 24V in our board
Auto Leveling


Board: 2 copper layers, 70.5 x 95.8 mm, 87 parts (1 on the bottom side), 79 nets.

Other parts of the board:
U$5: SIGMA_LOGO

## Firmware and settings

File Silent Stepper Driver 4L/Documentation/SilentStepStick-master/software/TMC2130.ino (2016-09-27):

/*
  Trinamic TMC2130 Example
*/

#include "SPI.h"

// Note: You also have to connect GND, 5V and VM.
//       A connection diagram can be found in the schematics.
#define EN_PIN    7 //enable (CFG6)
#define DIR_PIN   8 //direction
#define STEP_PIN  9 //step

#define CS_PIN   10 //chip select
#define MOSI_PIN 11 //SDI/MOSI (ICSP: 4, Uno: 11, Mega: 51)
#define MISO_PIN 12 //SDO/MISO (ICSP: 1, Uno: 12, Mega: 50)
#define SCK_PIN  13 //CLK/SCK  (ICSP: 3, Uno: 13, Mega: 52)

//TMC2130 registers
#define WRITE          0x80 //write flag
#define REG_GCONF      0x00
#define REG_GSTAT      0x01
#define REG_IHOLD_IRUN 0x10
#define REG_CHOPCONF   0x6C
#define REG_COOLCONF   0x6D
#define REG_DCCTRL     0x6E
#define REG_DRVSTATUS  0x6F

uint8_t tmc_write(uint8_t cmd, uint32_t data)
{
  uint8_t s;

  digitalWrite(CS_PIN, LOW);

  s = SPI.transfer(cmd);
  SPI.transfer((data>>24UL)&0xFF)&0xFF;
  SPI.transfer((data>>16UL)&0xFF)&0xFF;
  SPI.transfer((data>> 8UL)&0xFF)&0xFF;
  SPI.transfer((data>> 0UL)&0xFF)&0xFF;

  digitalWrite(CS_PIN, HIGH);

  return s;
}

uint8_t tmc_read(uint8_t cmd, uint32_t *data)
{
  uint8_t s;

  tmc_write(cmd, 0UL); //set read address

  digitalWrite(CS_PIN, LOW);

  s = SPI.transfer(cmd);
  *data  = SPI.transfer(0x00)&0xFF;
  *data <<=8;
  *data |= SPI.transfer(0x00)&0xFF;
  *data <<=8;
  *data |= SPI.transfer(0x00)&0xFF;
  *data <<=8;
  *data |= SPI.transfer(0x00)&0xFF;

  digitalWrite(CS_PIN, HIGH);

  return s;
}

void setup()
{
  //set pins
  pinMode(EN_PIN, OUTPUT);
  digitalWrite(EN_PIN, HIGH); //deactivate driver (LOW active)
  pinMode(DIR_PIN, OUTPUT);
  digitalWrite(DIR_PIN, LOW); //LOW or HIGH
  pinMode(STEP_PIN, OUTPUT);
  digitalWrite(STEP_PIN, LOW);

  pinMode(CS_PIN, OUTPUT);
  digitalWrite(CS_PIN, HIGH);
  pinMode(MOSI_PIN, OUTPUT);
  digitalWrite(MOSI_PIN, LOW);
  pinMode(MISO_PIN, INPUT);
  digitalWrite(MISO_PIN, HIGH);
  pinMode(SCK_PIN, OUTPUT);
  digitalWrite(SCK_PIN, LOW);

  //init serial port
  Serial.begin(9600); //init serial port and set baudrate
  while(!Serial); //wait for serial port to connect (needed for Leonardo only)
  Serial.println("\nStart...");

  //init SPI
  SPI.setDataMode(SPI_MODE3);
  SPI.setBitOrder(MSBFIRST);
  SPI.setClockDivider(SPI_CLOCK_DIV128);
  SPI.begin();

  //set TMC2130 config
  tmc_write(WRITE|REG_GCONF,      0x00000001UL); //voltage on AIN is current reference
  tmc_write(WRITE|REG_IHOLD_IRUN, 0x00001010UL); //IHOLD=0x10, IRUN=0x10
  tmc_write(WRITE|REG_CHOPCONF,   0x00008008UL); //native 256 microsteps

  //TMC2130 outputs on (LOW active)
  digitalWrite(EN_PIN, LOW);
}

void loop()
{
  static uint32_t last_time=0;
  uint32_t ms = millis();
  uint32_t data;
  uint8_t s;
    
  if((ms-last_time) > 1000) //run every 1s
  {
    last_time = ms;

    //show REG_GSTAT
    s = tmc_read(REG_GSTAT, &data);
    Serial.print("GSTAT:     0x0");
    Serial.print(data, HEX);
    Serial.print("\t - ");
    Serial.print("Status: 0x");
    Serial.print(s, HEX);
    if(s & 0x01) Serial.print(" reset");
    if(s & 0x02) Serial.print(" error");
    if(s & 0x04) Serial.print(" sg2");
    if(s & 0x08) Serial.print(" standstill");
    Serial.println(" ");

    //show REG_DRVSTATUS
    s = tmc_read(REG_DRVSTATUS, &data);
    Serial.print("DRVSTATUS: 0x");
    Serial.print(data, HEX);
    Serial.print("\t - ");
    Serial.print("Status: 0x");
    Serial.print(s, HEX);
    if(s & 0x01) Serial.print(" reset");
    if(s & 0x02) Serial.print(" error");
    if(s & 0x04) Serial.print(" sg2");
    if(s & 0x08) Serial.print(" standstill");
    Serial.println(" ");
  }

  //make steps
  digitalWrite(STEP_PIN, HIGH);
  delayMicroseconds(10);
  digitalWrite(STEP_PIN, LOW);
  delayMicroseconds(10);
}

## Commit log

2014-11-21 Adding the first files to git.This is the revision A of the boards
    [BCN3D++.brd, BCN3D++.sch, DRILEGEND.CFG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]
2014-11-21 Main Board almost ready
    5V rail to ICSP and some headers left to connect
    [BCN3D++.brd, BCN3D++.sch]
2014-11-25 New File Tree and Updates
    [BCN3D electronics.GBL, BCN3D electronics.GBO, BCN3D electronics.GBP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]
2014-12-24 Updates!
    Rev_A Ready and firsts prototypes
    [BCN3D electronics.brd, BCN3D electronics.sch, BCNmk2.brd]
2014-12-29 Updated files
    [BCN3D electronics.brd, BCN3D electronics.sch, mk2i.brd]
2015-02-13 The new REV_B has been shipped to production
    New MainBoard Design, new Stepper drivers and new Extruder Board.
    We also added many new components and configurations
    [BCN3D electronics.GBL, BCN3D electronics.GBO, BCN3D electronics.GBP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]
2016-04-08 BCN3D Electronics REV.E tested and manufactured
    [BCN3D electronics.GBL, BCN3D electronics.GBO, BCN3D electronics.GBP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]
2016-05-11 Fixed thermistor series resistors
    Added new license info and WEEE/FCC/CE Logo.
    [BCN3D electronics.brd, BCN3D electronics.sch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]
2016-09-27 Extruder board REV. F now on production
    New Extruder Board design for the late 2016 BCN3D Sigma 3D Printer
    [Extruder Board_centroid.csv, Smart Extruder Board.brd, Smart Extruder Board.sch]
2016-09-27 Silent Stepper Driver TMC2130 based REV.B
    2 Layer board for the TMC2130 based Stepper Driver board
    [BOM_v0.91.xlsx, Silent Stepper Driver.brd, Silent Stepper Driver.sch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]
2016-10-24 Update Ignore File and delete Eagle Lock files
    [filamentDetector.sch]
2016-11-02 Motherboard updated to new version REV.G
    Basically the only change in REV.G is the 20 contacts Flat Flexible
    Cable connector.
    [BCN3D electronics.brd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]
2017-02-09 File for the REV.H
    Files from the REV.H Released with new and more documentation.
    [BOM_v0.91.xlsx, DRILEGEND.CFG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]
2017-02-09 Added GERBER Files
    [BCN3D Electronics BOM REV_H.xlsx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]
2017-04-11 New SD Reader
    Add first revision files REVA
    [SD_Reader.csv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]

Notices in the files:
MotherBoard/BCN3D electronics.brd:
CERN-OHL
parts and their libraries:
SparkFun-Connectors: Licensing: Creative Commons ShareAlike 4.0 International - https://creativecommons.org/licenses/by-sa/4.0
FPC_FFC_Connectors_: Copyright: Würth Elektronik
